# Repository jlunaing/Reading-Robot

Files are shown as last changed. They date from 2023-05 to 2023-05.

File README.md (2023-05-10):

### Reading-Robot
A socially assistive robot that can help students with reading practice. For 
instructions on how to use the system, see [user guide](user_guide.md).

## Background

There is an insufficient availability of human experts to assist students in 
reading competency and comprehension. The goal of this porject is to create an 
socially assistive robot that can be used by therapists, teachers, and parents 
to help children and adults develop and practice reading comprehension skills 
while they do not have access to specialists. This robot enables the user to 
improve their reading skills without an educator present and allows educators to 
review the student's performance remotely. 

The design includes a robot and a phone running an app. The basic tasks that the
robot performs is to give instructions for the reading sessions and prompts the
student to start reading. The robot then records the passage read to allow a 
teacher or therapist to review it at a later time. Then, the robot asks 
questions based on the reading and gives constructive feedback based on the 
correctness of the responses. During the interaction, the robot has the ability
to tilt the phone back and forth, wiggle its antennas, and show different faces
on its LED screen. This gives the interaction with the user more embodiment.

## Making a Reading Robot

### Part List
To make one of this robots, the following parts are needed:

#### General parts:
- 3D printed parts (see [CAD files](src/hardware/cad/solidworks/))
- Android phone (1)
- Bluetooth headset (optional) (1)
- Pimoroni Unicorn Hat HD LED array (1)					

#### Actuation:
- TowerPro MG995 Digital servo motor (1)				
- Uxcell 6V DC motor, 100-rpm (1)	
- Adafruit TB6612 motor driver board (1)					
- 6455K13 plastic ball bearing (2)					
- RB-Tib-11 Lynxmotion servo timing belt pulley (2)					
- 1254N22 MXL timing belt pulley (1)	

#### Fasteners:
- Tapered heat-set inserts:
  - 2-56 thread size (93365A110)			
  - 4-40 thread size (93365A120)
- Screws:
  - 18-8 screw 1/2'' long (91772A110)
  - 2-56 screw 11/32'' long (91772A506)
  - 2-56 screw 3/16'' long (91772A076)
  - 4-40 screw 3/4'' long (91772A113)			
- Neodymium magnet 1/4'' (5862K103) (8)
- 18-8 binding barrel & screw (99637A307) (1)
- Nylon spacers (90176A114)
- 5/8'' Long Dowel Pin (98381A539)					
- 2 – 1/8'' Long Dowel Pin (98381A325)					

#### Electronics:
- Raspberry Pi 4 + SD card
- Custom PCB for power distribution (see [board files](src/hardware/pcb/))
- 40-pin connector (S9200-ND) (2)
- USB-C breakout board (1568-1958-ND)
- JST RCY connector, 2-pin (PRT-10501)					
- JST jumper 2-wire (PRT-09914)					
- JST jumper 3-wire (PRT-09915)

### Power:
- AUKEY USB-C 2 port charger					
- AC adapter/power supply (2)					
- USB 3.1 type C M-F data extension cable (2)					

The assembly of the robot can be facilitated by refering to the assembly drawings
or the [CAD files](src/hardware/cad/solidworks/). Some reference images are 
included below.

<p align="center">
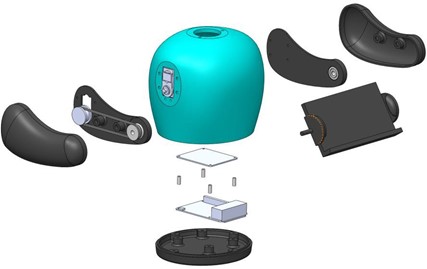
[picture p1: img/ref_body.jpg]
Body assembly
    
</p>

<p align="center">
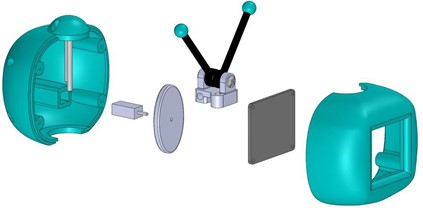
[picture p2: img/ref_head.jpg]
Head assembly
    
</p>

### Code

See [source files](src/firmware/python/) for details.

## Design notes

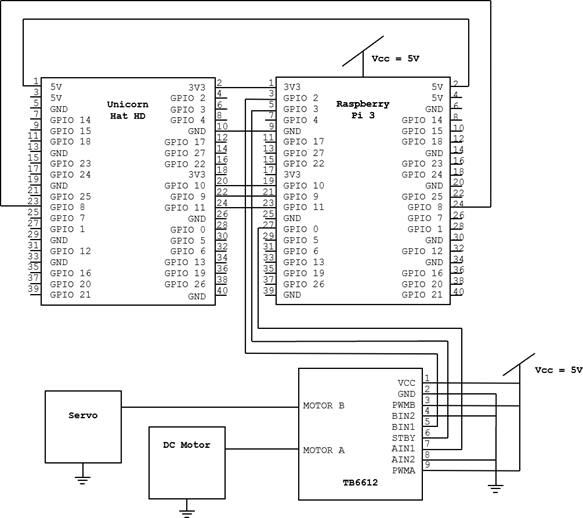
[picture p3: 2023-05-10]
img/ref_schematic.png

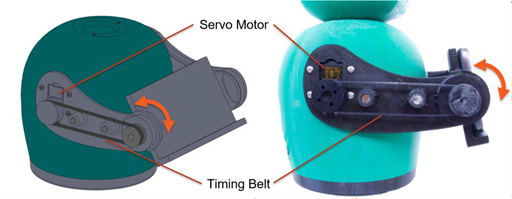
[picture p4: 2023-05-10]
img/ref_servo.png

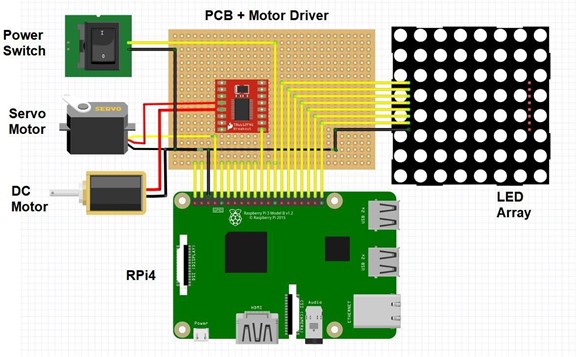
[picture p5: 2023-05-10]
img/ref_connections.jpg

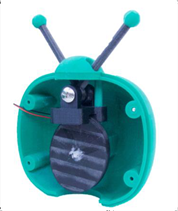
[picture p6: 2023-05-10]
img/ref_antenna_02.png

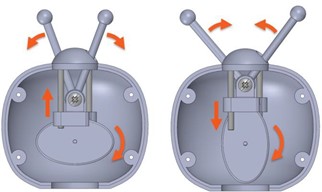
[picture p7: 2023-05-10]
img/ref_antenna_01.jpg

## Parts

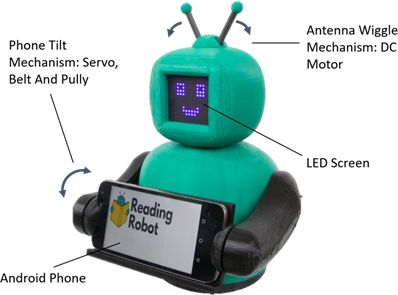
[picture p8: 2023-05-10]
img/ref_parts.png

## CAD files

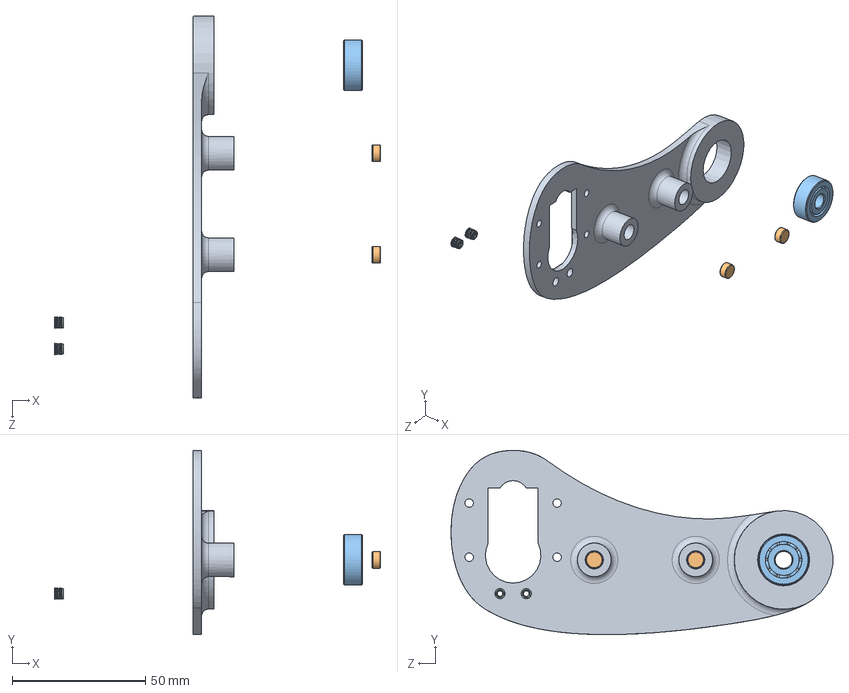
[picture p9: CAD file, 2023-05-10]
src/hardware/cad/solidworks/arm_base_right_assy.SLDASM
122.5 x 69.2 x 143.5 mm
5862K103_HIGH-PULL RARE EARTH MAGNETIC DISC x 2
6455K130_GENERAL PURPOSE PLASTIC BALL BEARING
arm_base_right
93365A120_HEAT-SET INSERTS FOR PLASTICS x 2

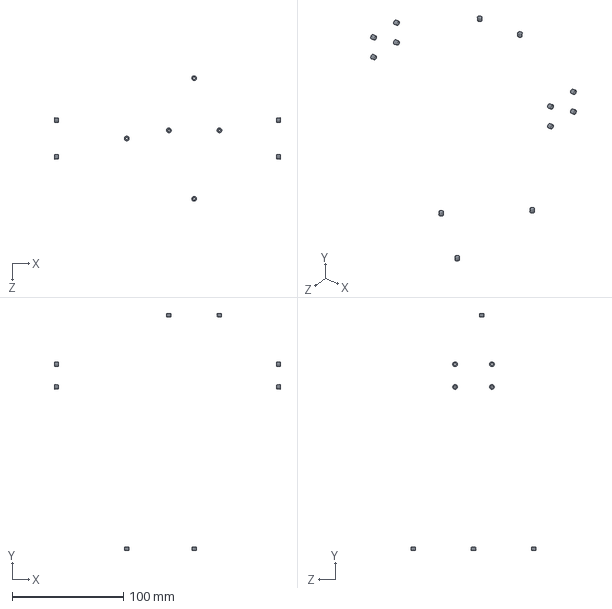
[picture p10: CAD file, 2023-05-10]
src/hardware/cad/solidworks/body_top_with_inserts.SLDASM
202.8 x 212.9 x 112.6 mm
93365A120_HEAT-SET INSERTS FOR PLASTICS x 13

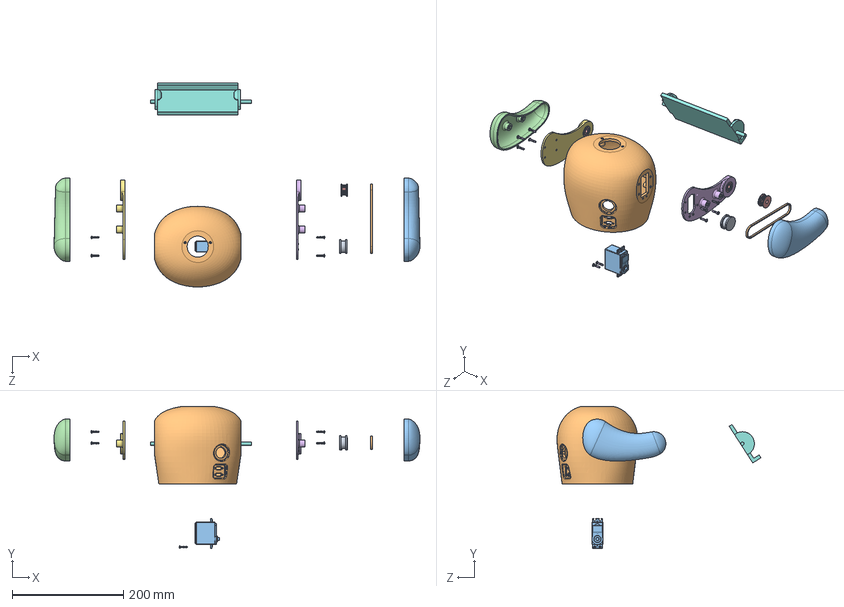
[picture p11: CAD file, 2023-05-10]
src/hardware/cad/solidworks/body_top_assy.SLDASM
658.0 x 255.6 x 366.7 mm
93365A120_HEAT-SET INSERTS FOR PLASTICS x 15
body_top
servomotor
5862K103_HIGH-PULL RARE EARTH MAGNETIC DISC x 8
6455K130_GENERAL PURPOSE PLASTIC BALL BEARING x 2
arm_base_right
arm_base_left
phone holder
servo_timing_belt_pulley
belt
arm_cover_right
arm_cover_left
1254N220_MXL SERIES LIGHTWEIGHT TIMING BELT PULLEY
91772A110_18-8 SS PAN HEAD PHILLIPS MACHINE SCREW x 10

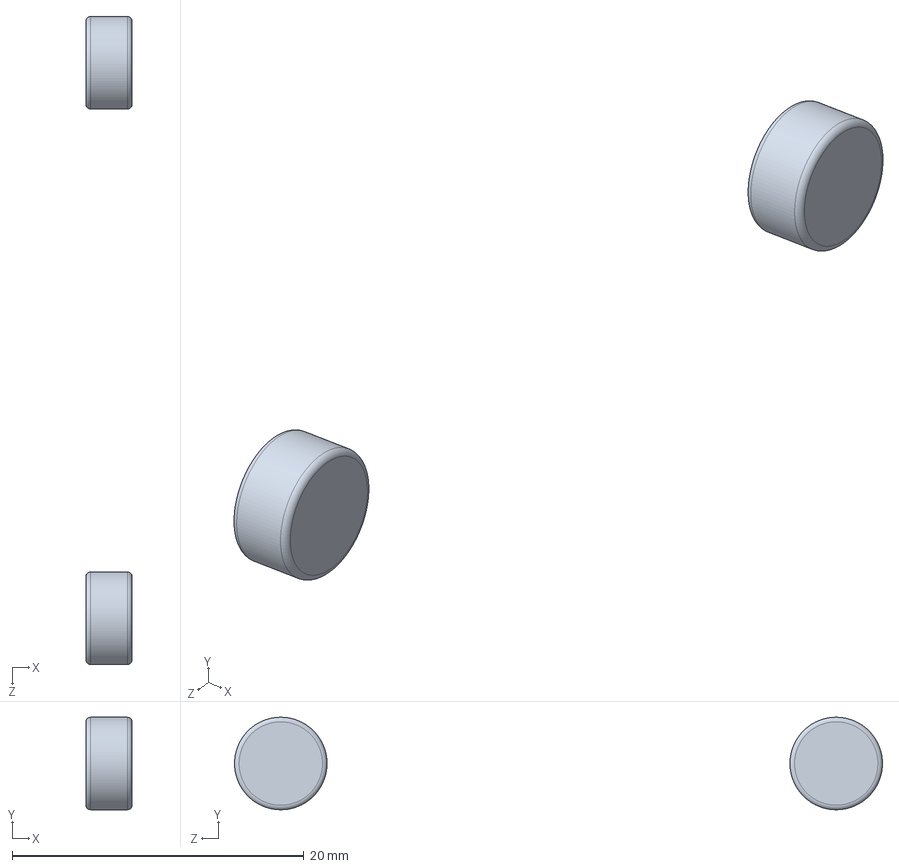
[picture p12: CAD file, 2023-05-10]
src/hardware/cad/solidworks/arm_cover_left_assy.SLDASM
3.17 x 6.35 x 44.5 mm
5862K103_HIGH-PULL RARE EARTH MAGNETIC DISC x 2

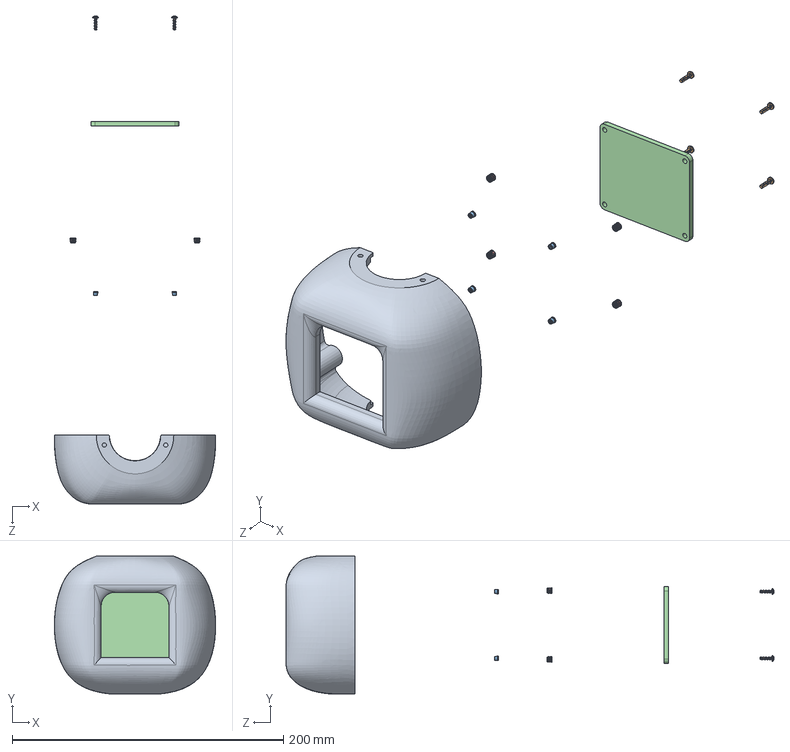
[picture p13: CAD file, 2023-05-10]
src/hardware/cad/solidworks/head_front_assy.SLDASM
119.0 x 101.6 x 359.9 mm
head_front
91772A506_PASSIVATED 18-8 SS PAN HEAD PHILLIPS SCREW x 4
93365A110_HEAT-SET INSERTS FOR PLASTICS x 4
led_screen
93365A120_HEAT-SET INSERTS FOR PLASTICS x 4

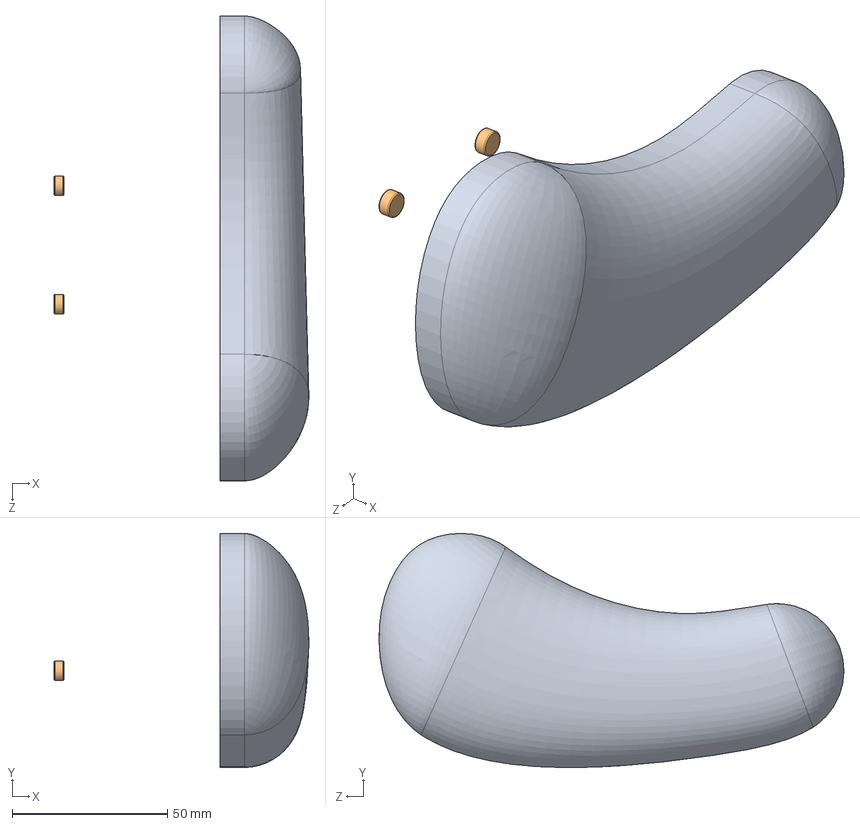
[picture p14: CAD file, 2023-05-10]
src/hardware/cad/solidworks/arm_cover_right_assy.SLDASM
82.0 x 75.3 x 149.6 mm
arm_cover_right
5862K103_HIGH-PULL RARE EARTH MAGNETIC DISC x 2

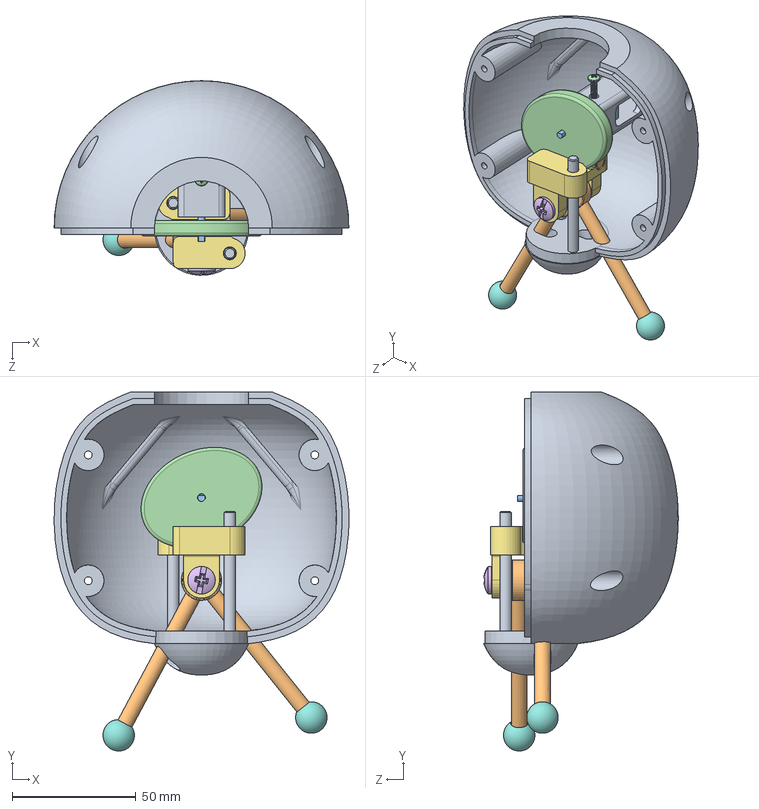
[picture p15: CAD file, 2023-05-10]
src/hardware/cad/solidworks/head_back_assy.SLDASM
119.0 x 144.9 x 78.6 mm
head_back
antenna_bottom x 2
dc_motor
crank
98002A709_STEEL BINDING SCREWS
99637A212_18-8 STAINLESS STEEL BINDING BARREL
antenna fixture
antenna_top x 2
98381A325_DOWEL PIN x 2
98381A539_ALLOY STEEL DOWEL PIN x 2
93365A120_HEAT-SET INSERTS FOR PLASTICS
91772A110_18-8 SS PAN HEAD PHILLIPS MACHINE SCREW

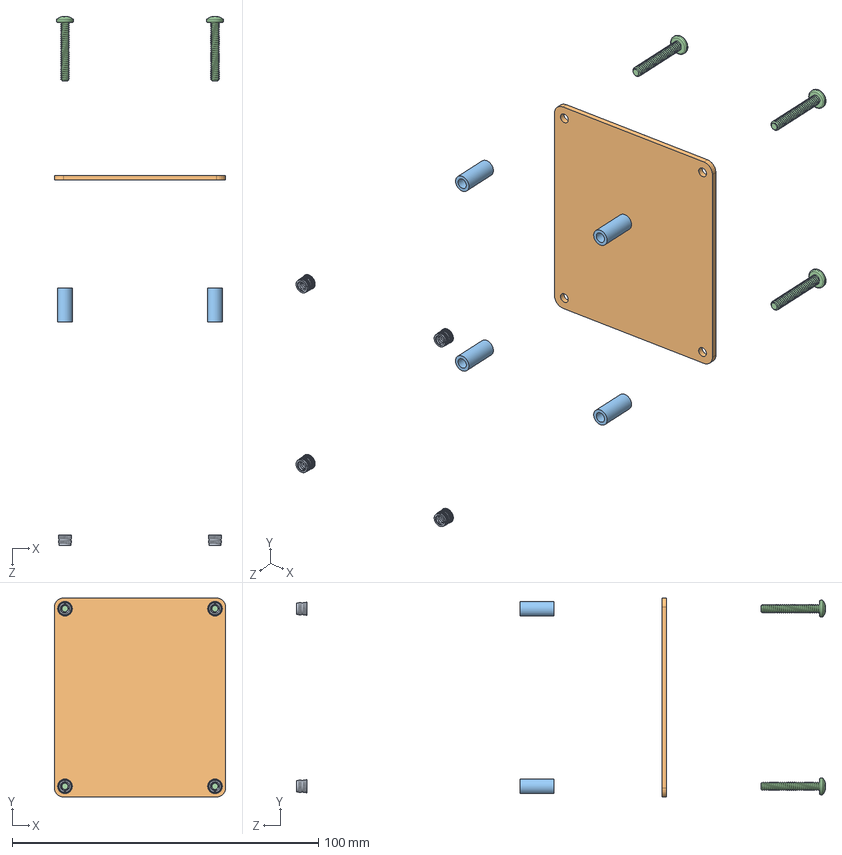
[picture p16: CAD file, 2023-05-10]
src/hardware/cad/solidworks/body_bottom_assy.SLDASM
56.0 x 65.0 x 172.8 mm
93365A120_HEAT-SET INSERTS FOR PLASTICS x 4
PCB
90176A114_NYLON UNTHREADED SPACERS x 4
91772A113_18-8 SS PAN HEAD PHILLIPS MACHINE SCREW x 4

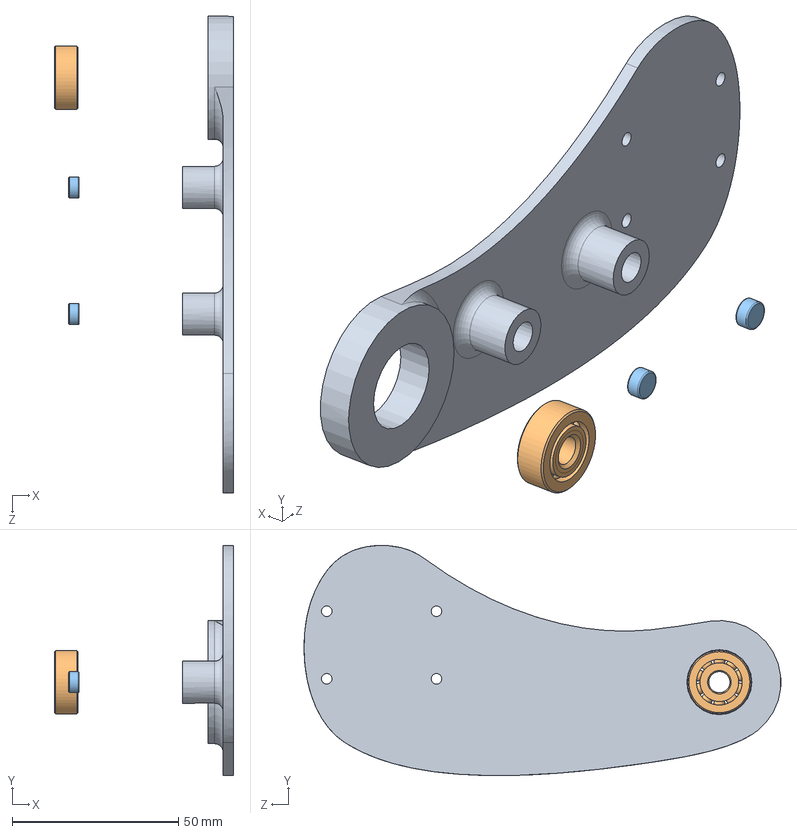
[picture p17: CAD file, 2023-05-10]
src/hardware/cad/solidworks/arm_base_left_assy.SLDASM
54.0 x 69.2 x 143.5 mm
arm_base_left
6455K130_GENERAL PURPOSE PLASTIC BALL BEARING
5862K103_HIGH-PULL RARE EARTH MAGNETIC DISC x 2

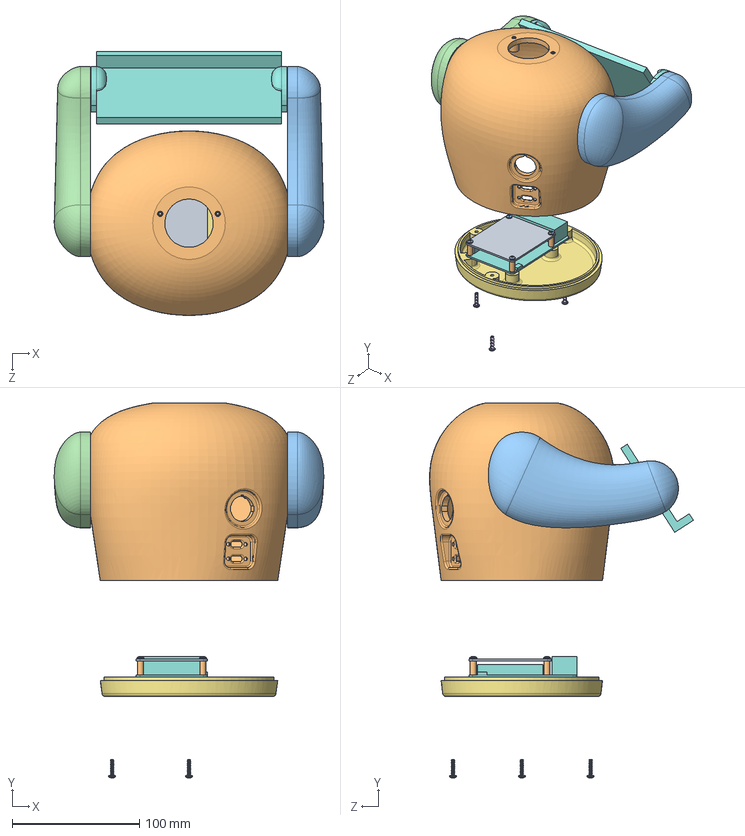
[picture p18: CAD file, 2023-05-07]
src/hardware/cad/solidworks/body_main.SLDASM
212.1 x 294.9 x 207.6 mm
93365A120_HEAT-SET INSERTS FOR PLASTICS x 20
body_top_3
kiso
5862K103_HIGH-PULL RARE EARTH MAGNETIC DISC x 8
6455K130_GENERAL PURPOSE PLASTIC BALL BEARING x 2
arm_base_right_3
arm_base_left_2
phone holder_3
Servo Timing Belt Pulley
Belt
arm_cover_right_2
arm_cover_left_2
1254N220_MXL SERIES LIGHTWEIGHT TIMING BELT PULLEY
91772A110_18-8 SS PAN HEAD PHILLIPS MACHINE SCREW x 13
body_bottom_4
Rasberry pi
PCB
90176A114_NYLON UNTHREADED SPACERS x 4
91772A113_18-8 SS PAN HEAD PHILLIPS MACHINE SCREW x 4

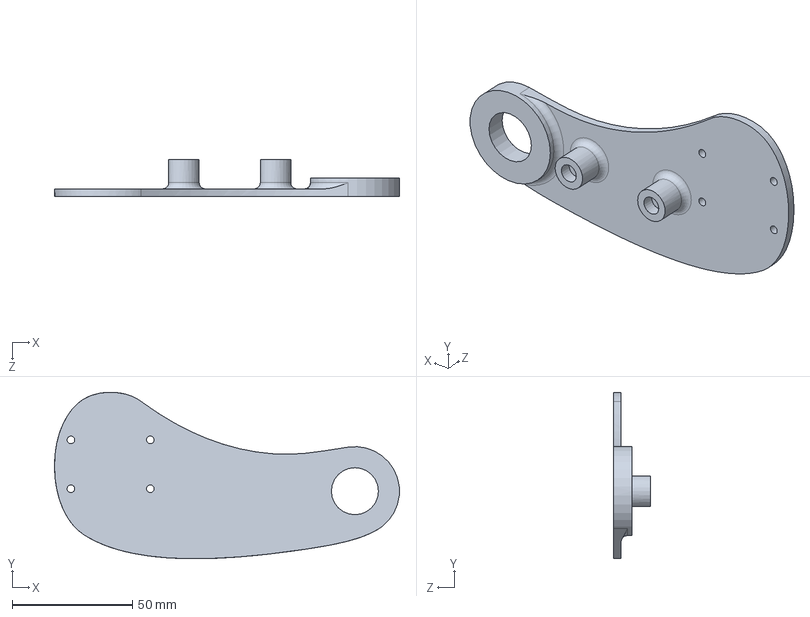
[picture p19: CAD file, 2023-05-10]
src/hardware/cad/solidworks/arm_base_left.SLDPRT
143.5 x 69.2 x 15.4 mm

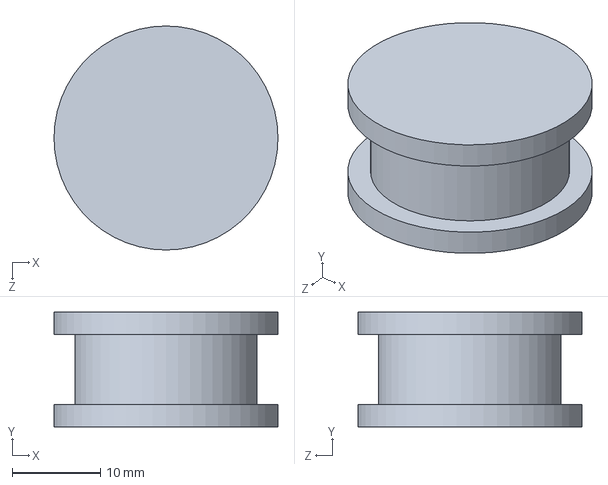
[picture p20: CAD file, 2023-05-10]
src/hardware/cad/solidworks/servo_timing_belt_pulley.SLDPRT
25.4 x 13.0 x 25.4 mm

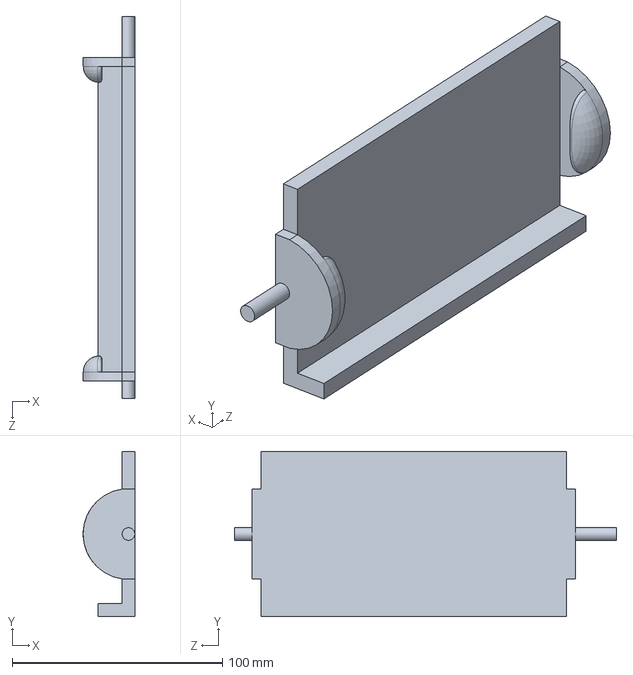
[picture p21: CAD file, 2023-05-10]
src/hardware/cad/solidworks/phone holder.SLDPRT
24.6 x 78.5 x 181.6 mm

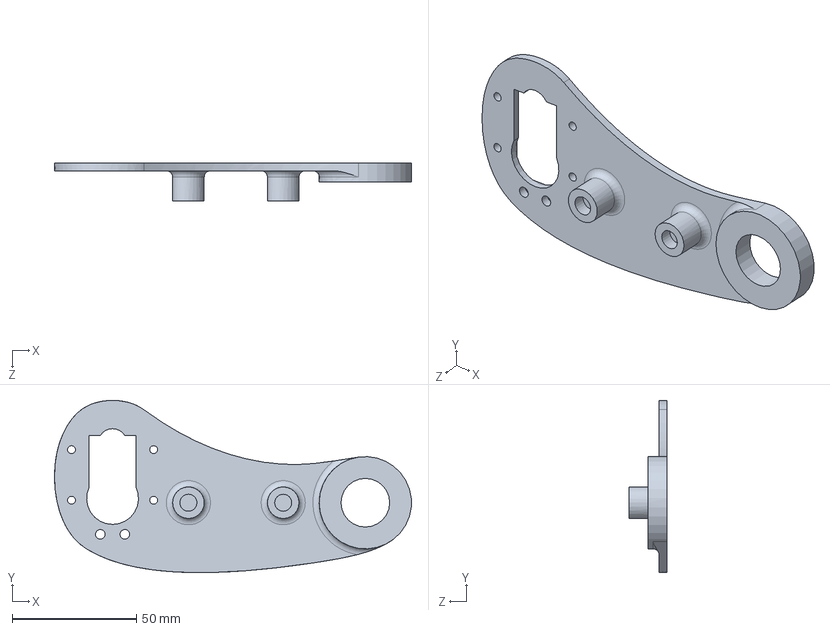
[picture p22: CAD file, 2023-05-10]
src/hardware/cad/solidworks/arm_base_right.SLDPRT
143.5 x 69.2 x 15.4 mm

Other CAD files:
src/hardware/cad/solidworks/PCB.SLDPRT
src/hardware/cad/solidworks/arm_cover_right.SLDPRT
src/hardware/cad/solidworks/servomotor.SLDPRT
src/hardware/cad/solidworks/belt.SLDPRT
src/hardware/cad/solidworks/1254N220_MXL SERIES LIGHTWEIGHT TIMING BELT PULLEY.SLDPRT
src/hardware/cad/solidworks/5862K103_HIGH-PULL RARE EARTH MAGNETIC DISC.SLDPRT
src/hardware/cad/solidworks/6455K130_GENERAL PURPOSE PLASTIC BALL BEARING.SLDPRT
src/hardware/cad/solidworks/90176A114_NYLON UNTHREADED SPACERS.SLDPRT
src/hardware/cad/solidworks/91772A110_18-8 SS PAN HEAD PHILLIPS MACHINE SCREW.SLDPRT
src/hardware/cad/solidworks/91772A113_18-8 SS PAN HEAD PHILLIPS MACHINE SCREW.SLDPRT
src/hardware/cad/solidworks/91772A506_PASSIVATED 18-8 SS PAN HEAD PHILLIPS SCREW.SLDPRT
src/hardware/cad/solidworks/93365A110_HEAT-SET INSERTS FOR PLASTICS.SLDPRT
src/hardware/cad/solidworks/93365A120_HEAT-SET INSERTS FOR PLASTICS.SLDPRT
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

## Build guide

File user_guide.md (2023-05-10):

### User Guide for the Reading Robot

1. [Set up](#set-up)
2. [Troubleshooting](#troubleshooting)

## Set up
1. Locate female USB-C ports on the back of the robot. The bottom port is dedicated to the Raspberry Pi and the one above is connected to the power distribution board.

<p align="center">
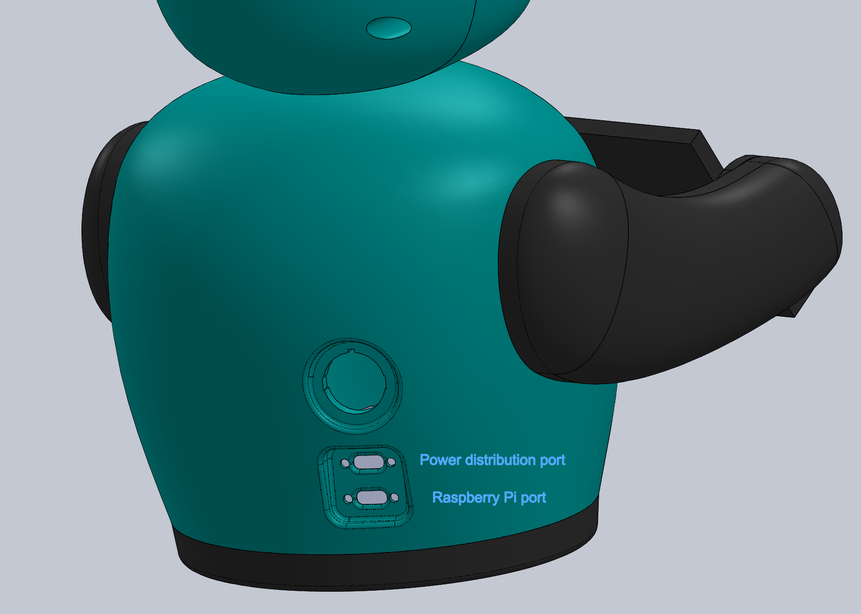
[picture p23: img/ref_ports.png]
Input ports for the robot.
    
</p>

2. Connect the Raspberry Pi port to power. To verify, you will see a red glow inside the robot.
3. Wait for a blue, happy face to appear on LED Array. This is important as it is an indicator that the serial port service has been registered and that GPIOs are reset.
4. Connect the power distribution board to power. 
5. If using a wireless headset, connect it to the Android through Bluetooth. During the first time, you will have to pair the headset to the phone. Later usage should connect the headset to the phone seamlessly.
   
Once this has all been completed, the robot should be ready to go. Now, you can open the phone app.

1. Open the [app](src/firmware/appinventor/) on the phone.
2. Once opened, a “connected” notification should show up fairly quickly to let the user know they are connected to Bluetooth. If this does not happen, you can press the robot's picture once the robot finishes its introduction dialogue. 
    - If a face change does not occur after introduction, Bluetooth is not connected and a notification error will pop up on the app. 
    - Refer to the next section, troubleshooting.
3. When the connected notifier appears, the app is ready to go. The user will read (press "begin reading" to start reading and "stop reading" to proceed to the next part) and answer questions afterwards (press "question" button).

<p align="center">
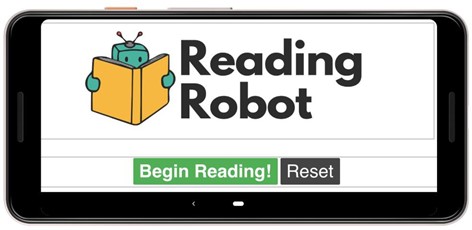
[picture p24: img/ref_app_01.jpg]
Android app intro screen.
    
</p>

After the session is over:

1. Close the app and make sure to end it completely.
2. Turn off the PCB *first*. The robot does not like it when you power down the Raspberry Pi first.
   - This is currently an issue because the PCB has its I/O pins for the motors routed to the pins on the RPi that give a 3.3-V voltage on startup.
   - This is also the same reason why the PCB is turned on after the RPi’s startup sequence. 
3. Turn off the Raspberry Pi.

Optional step for users, parents, instructors, and educators:

1. To playback the audio file that was generated from the app stored in the phone, go to the storage settings of your phone and search for the generated "Reading Robot Study 2020" folder. The default file name is `mysound.3gp`. Make sure to look at the time associated with the file creation to see which corresponds to which user.
2. To view the text file that was generated from the app during the human-robot interaction, go to the storage settings and look for the corresponding `.txt` file.

## Troubleshooting

This section discusses some of the problems that could be encountered while
working with the robot as it relates to the **Bluetooth connection**.

If the Bluetooth connection doesn’t happen, it could be for a multitude of reasons. The first possible error is that the Raspberry Pi is no longer paired with the Android phone. To check for this, go to your phone settings and check for the Bluetooth paired devices. Under the “paired devices” section, there should a paired device corresponding to the Raspberry Pi used.

If this device is not there or no longer paired, you must direct your attention to the Raspberry Pi. Unscrew the bottom of the robot and connect to the Pi. After the Pi has turned on, it should show up in the “available devices” section of the
phone's Bluetooth settings. Click on Raspberry Pi device on the phone. A notification should appear on the Pi’s home screen and phone screen for a pairing request. Press confirm. The device should now be paired, and the Bluetooth connection should work between the Pi and the app.

You can hardcode the process in the above paragraph as well in terminal: `bluetoothctl` $\to$ `agent on` $\to$ `discoverable on` $\to$ `scan on`. The phone's bluetooth address should appear. Pair it with the Pi and that should work.

If the Raspberry Pi is still paired, there are two reasons why there is no bluetooth connection between the devices. ***First***, the bluetooth address might be incorrect from the development environment (Kodular) side of things. Double check and make sure the address is correct. You can find the address of your Raspberry Pi in terminal using the `hciconfig` command in the terminal. Look for the address followed by `BD Address`.

If the address is correct, then the *second* possibility is that the user troubleshooting is not waiting long enough to connect the devices. After the blue, happy face screen appears, wait an additional 15-30 seconds.

If none of this works, there could be an issue with the serial port service registering. This is a Python script that runs on startup and gives access to the Raspberry Pi serial ports. The name of the script is `register.py` and can be found with all the other scripts the robot utilizes to function. You can check to see if it ran on startup as well as anything else that happens between the Android and Pi. Look up the `/home/pi/logs` directory. The file called `cronlog` will give you a log of what happens during the interaction between the phone and Raspberry Pi. This will be pretty important when troubleshooting the robot and changing the script.

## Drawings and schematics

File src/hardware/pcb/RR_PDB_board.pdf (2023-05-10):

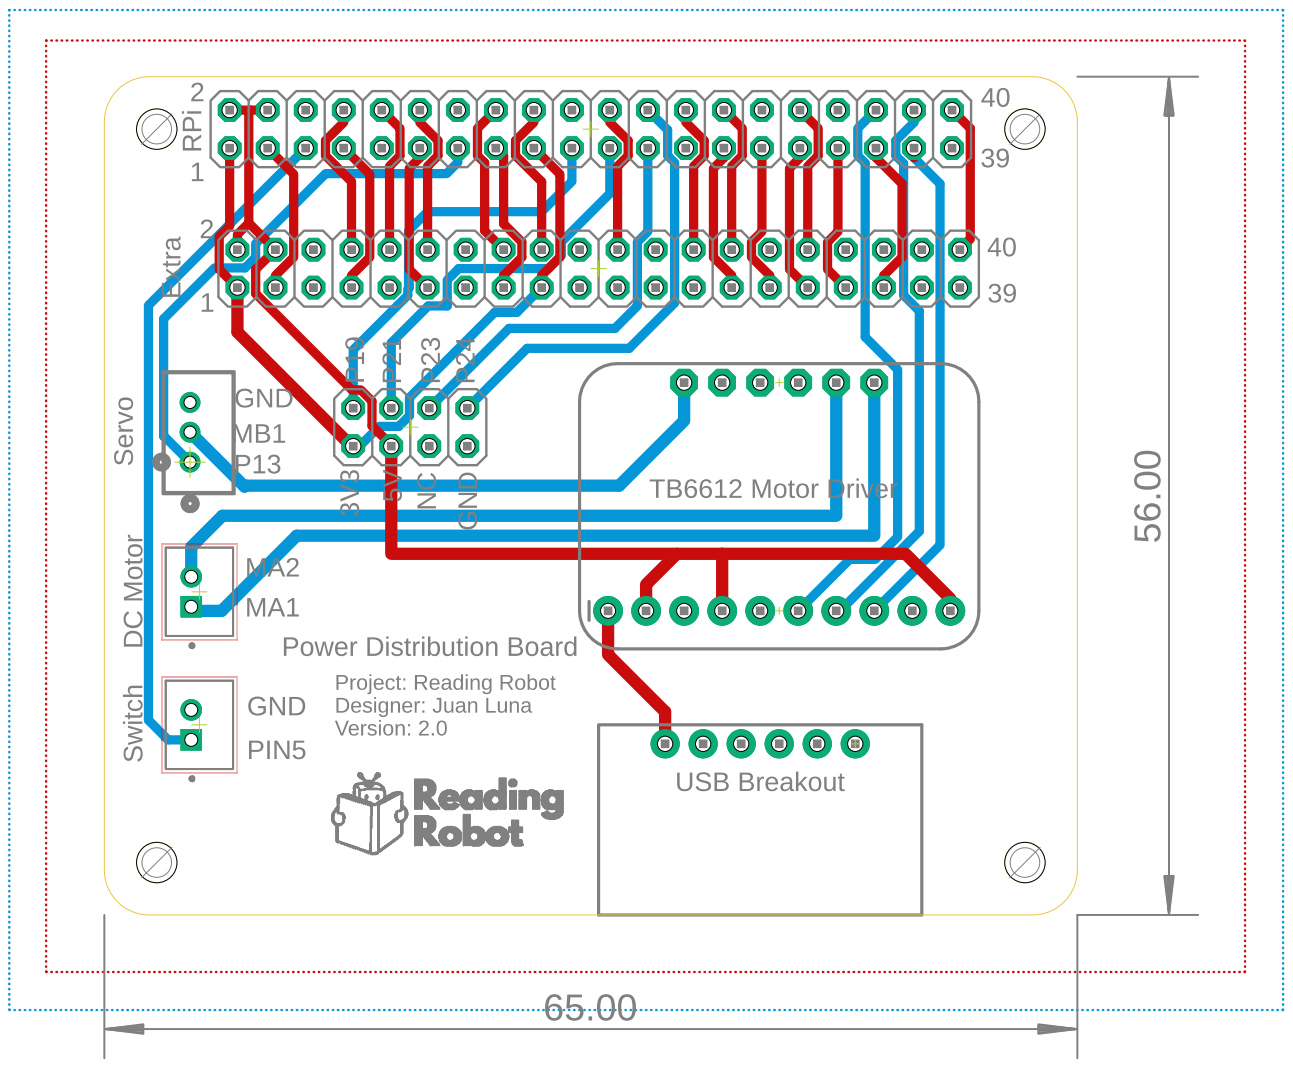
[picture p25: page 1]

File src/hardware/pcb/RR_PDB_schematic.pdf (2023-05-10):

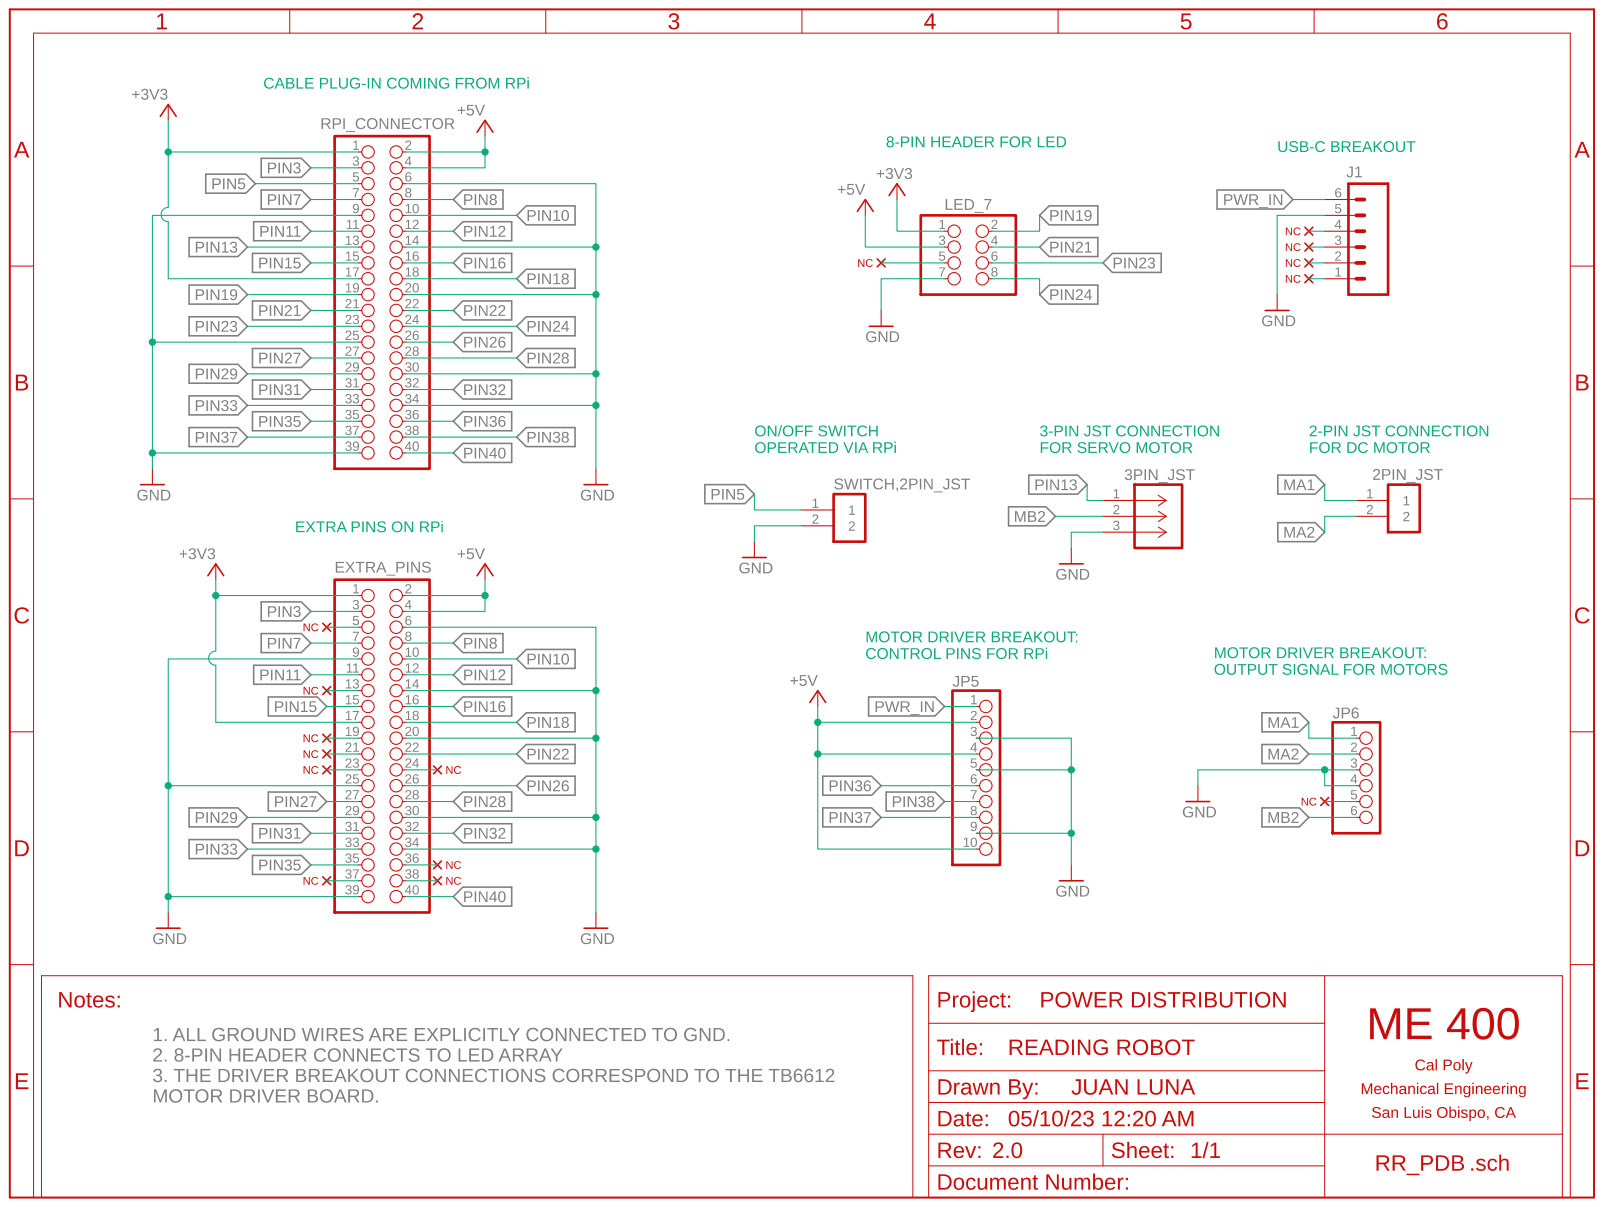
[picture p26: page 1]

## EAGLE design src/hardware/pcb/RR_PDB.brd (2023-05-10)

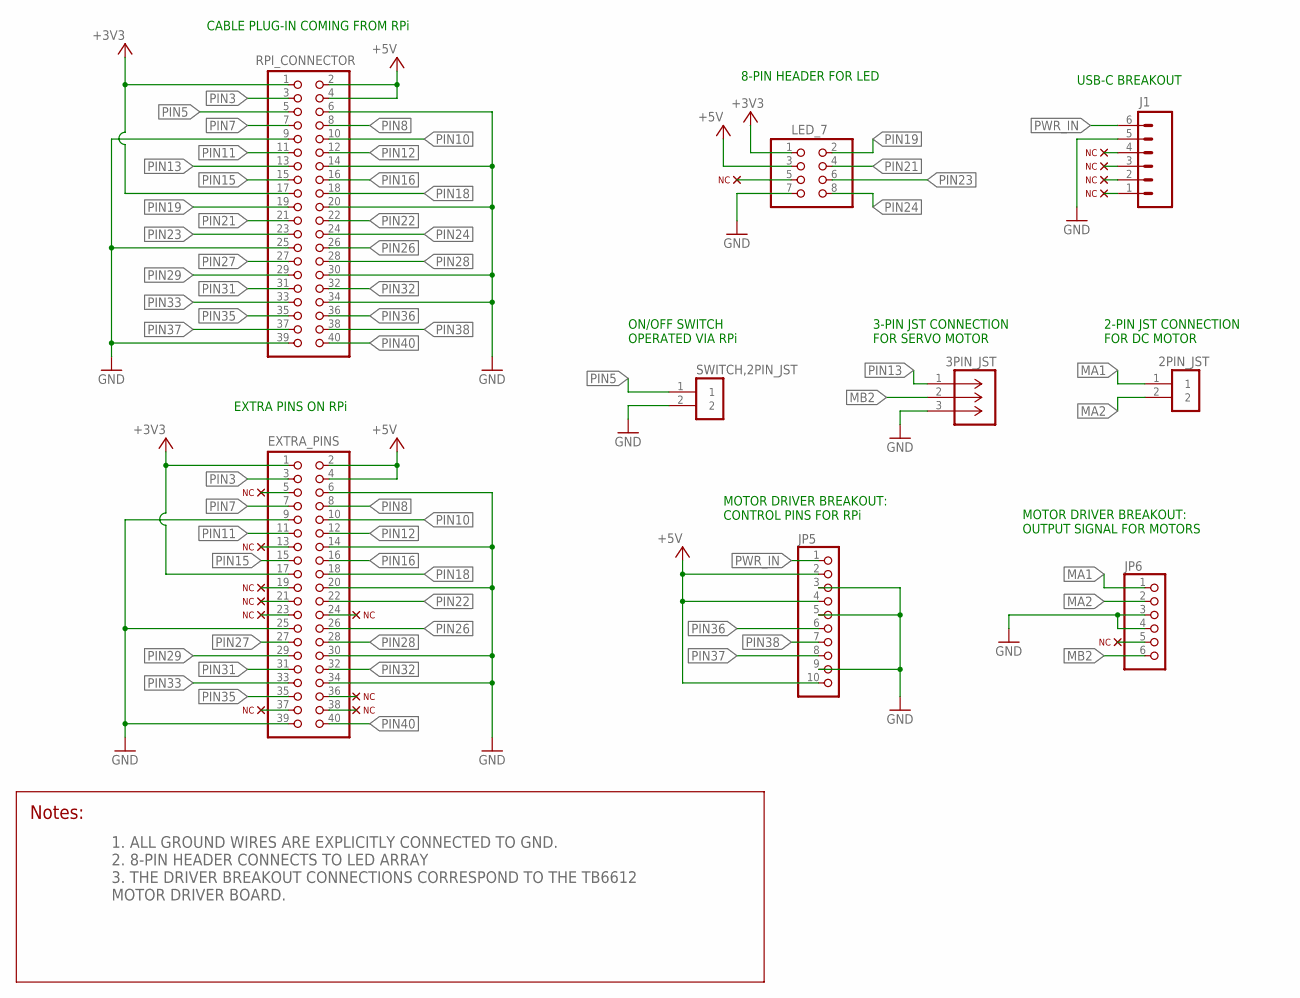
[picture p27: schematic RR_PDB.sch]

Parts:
2PIN_JST: B2B-PH-K-S(LF)(SN); JST_B2B-PH-K-S(LF)(SN)
3PIN_JST: B3B-PH-K-S(LF)(SN); CONN_B3B-PH-K-S(LF)(SN)_JST
EXTRA_PINS: PINHD-2X20; 2X20
J1: CONN_06NO_SILK_NO_POP; 1X06_NO_SILK
JP5: HEADER-1X10THICKER; 1X10_ROUND_76
JP6: PINHD-1X6CB; 1X06-CLEANBIG
LED_7: PINHD-2X4; 2X04
RPI_CONNECTOR: PINHD-2X20; 2X20
SWITCH,2PIN_JST: B2B-PH-K-S(LF)(SN); JST_B2B-PH-K-S(LF)(SN)

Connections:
+3V3: EXTRA_PINS.1, EXTRA_PINS.17, LED_7.1, RPI_CONNECTOR.1, RPI_CONNECTOR.17
+5V: EXTRA_PINS.2, EXTRA_PINS.4, JP5.2, JP5.4, JP5.10, LED_7.3, RPI_CONNECTOR.2, RPI_CONNECTOR.4
CC1: J1.4
CC2: J1.1
D+: J1.2
D-: J1.3
GND: 3PIN_JST.3, EXTRA_PINS.6, EXTRA_PINS.9, EXTRA_PINS.14, EXTRA_PINS.20, EXTRA_PINS.25, EXTRA_PINS.30, EXTRA_PINS.34, EXTRA_PINS.39, J1.5, JP5.3, JP5.5, JP5.9, JP6.3, JP6.4, LED_7.7, RPI_CONNECTOR.6, RPI_CONNECTOR.9, RPI_CONNECTOR.14, RPI_CONNECTOR.20, RPI_CONNECTOR.25, RPI_CONNECTOR.30, RPI_CONNECTOR.34, RPI_CONNECTOR.39, SWITCH,2PIN_JST.2
MA1: 2PIN_JST.1, JP6.1
MA2: 2PIN_JST.2, JP6.2
MB2: 3PIN_JST.2, JP6.6
PIN3: EXTRA_PINS.3, RPI_CONNECTOR.3
PIN5: RPI_CONNECTOR.5, SWITCH,2PIN_JST.1
PIN7: EXTRA_PINS.7, RPI_CONNECTOR.7
PIN8: EXTRA_PINS.8, RPI_CONNECTOR.8
PIN10: EXTRA_PINS.10, RPI_CONNECTOR.10
PIN11: EXTRA_PINS.11, RPI_CONNECTOR.11
PIN12: EXTRA_PINS.12, RPI_CONNECTOR.12
PIN13: 3PIN_JST.1, RPI_CONNECTOR.13
PIN15: EXTRA_PINS.15, RPI_CONNECTOR.15
PIN16: EXTRA_PINS.16, RPI_CONNECTOR.16
PIN18: EXTRA_PINS.18, RPI_CONNECTOR.18
PIN19: LED_7.2, RPI_CONNECTOR.19
PIN21: LED_7.4, RPI_CONNECTOR.21
PIN22: EXTRA_PINS.22, RPI_CONNECTOR.22
PIN23: LED_7.6, RPI_CONNECTOR.23
PIN24: LED_7.8, RPI_CONNECTOR.24
PIN26: EXTRA_PINS.26, RPI_CONNECTOR.26
PIN27: EXTRA_PINS.27, RPI_CONNECTOR.27
PIN28: EXTRA_PINS.28, RPI_CONNECTOR.28
PIN29: EXTRA_PINS.29, RPI_CONNECTOR.29
PIN31: EXTRA_PINS.31, RPI_CONNECTOR.31
PIN32: EXTRA_PINS.32, RPI_CONNECTOR.32
PIN33: EXTRA_PINS.33, RPI_CONNECTOR.33
PIN35: EXTRA_PINS.35, RPI_CONNECTOR.35
PIN36: JP5.6, RPI_CONNECTOR.36
PIN37: JP5.8, RPI_CONNECTOR.37
PIN38: JP5.7, RPI_CONNECTOR.38
PIN40: EXTRA_PINS.40, RPI_CONNECTOR.40
PWR_IN: J1.6, JP5.1

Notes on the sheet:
MOTOR DRIVER BREAKOUT: OUTPUT SIGNAL FOR MOTORS
MOTOR DRIVER BREAKOUT: CONTROL PINS FOR RPi
2-PIN JST CONNECTION FOR DC MOTOR
3-PIN JST CONNECTION FOR SERVO MOTOR
CABLE PLUG-IN COMING FROM RPi
ON/OFF SWITCH OPERATED VIA RPi
EXTRA PINS ON RPi
8-PIN HEADER FOR LED
USB-C BREAKOUT
1. ALL GROUND WIRES ARE EXPLICITLY CONNECTED TO GND. 2. 8-PIN HEADER CONNECTS TO LED ARRAY 3. THE DRIVER BREAKOUT CONNECTIONS CORRESPOND TO THE TB6612 MOTOR DRIVER BOARD.

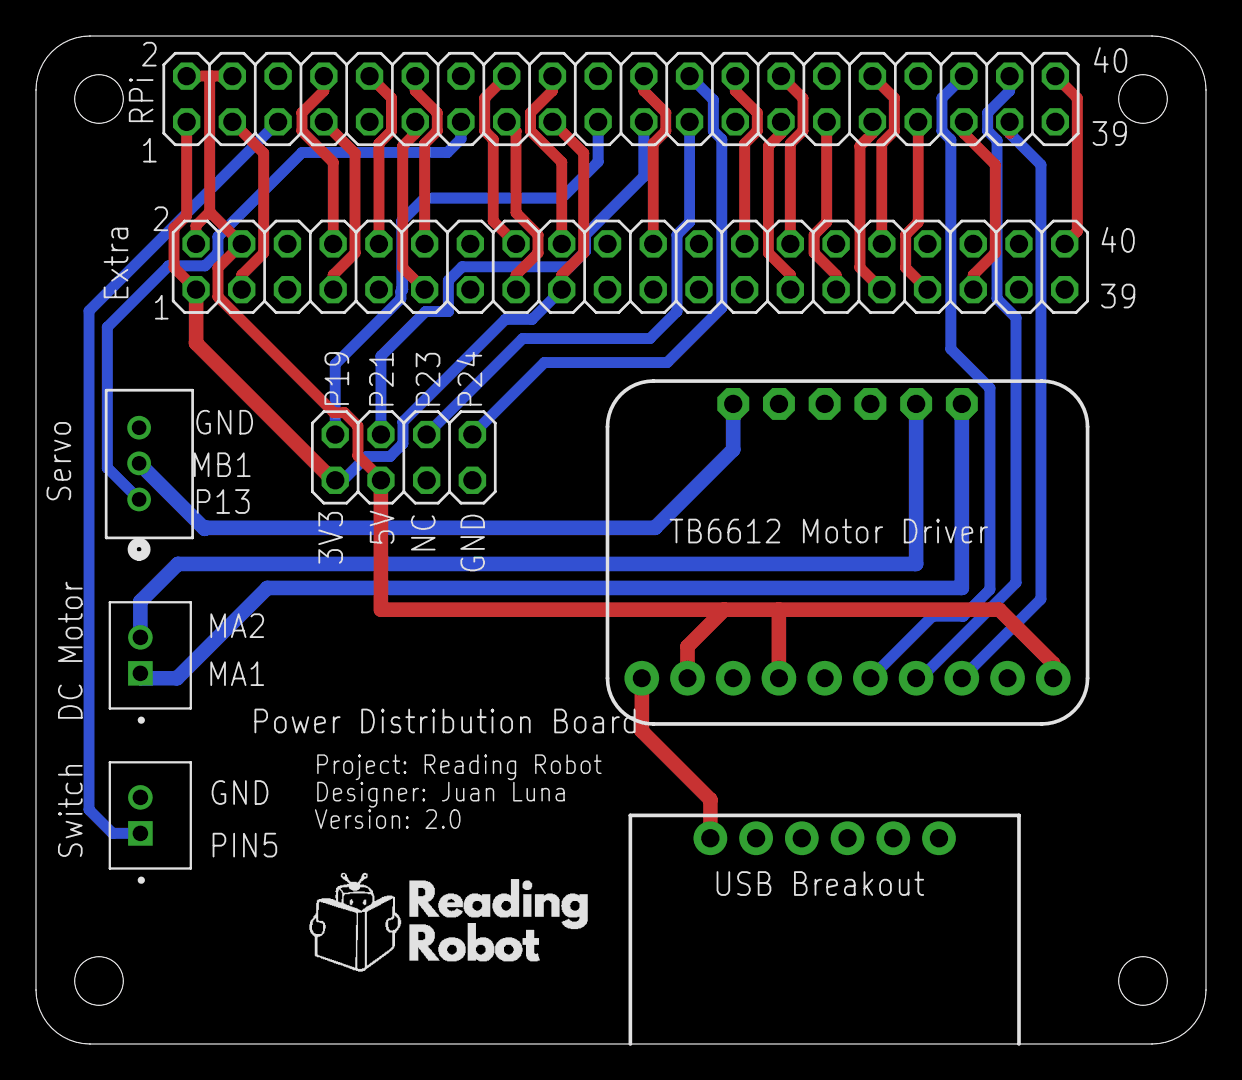
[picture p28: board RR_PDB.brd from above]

Board: 2 copper layers, 65.0 x 56.0 mm, 9 parts (0 on the bottom side), 35 nets.

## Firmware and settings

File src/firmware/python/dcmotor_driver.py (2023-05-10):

'''!    @file       dcmotor_driver.py
        @brief      Motor testing
        @details    This code will need to take in the following values: 
                    time for antenna move and position for servo. May need to 
                    saturate duty cycle.
        @author     Juan Luna
        @date       2021-01-28 Created
'''

import RPi.GPIO as GPIO
from time import sleep



# Pins for Motor Driver Inputs 
DCMotor = 0 #GPIO 0

ServoMotor = 1 #GPIO 1
ServoMotorEN = 2 #GPIO 2
STBYPin = 3 #GPIO 3

def setup():
    GPIO.setmode(GPIO.BCM)              # GPIO Numbering
    GPIO.setup(DCMotor,GPIO.OUT)  # All pins as Outputs
    
    GPIO.setup(ServoMotor,GPIO.OUT)
    GPIO.setup(ServoMotorEN,GPIO.OUT)
    servo_ctr = GPIO.PWM(ServoMotor, 50) #channel = ServoMotor, frequency=50Hz
    
    
    
    GPIO.setup(STBYPin,GPIO.OUT)   #enable motors
    GPIO.output(STBYPin,GPIO.HIGH)
 
def move_antenna():
    # Going forwards
    GPIO.output(DCMotor,GPIO.HIGH)
 
    sleep(5) # will need to remove this for cooperative multitasking
    # stop the motor after t= 5 seconds
    GPIO.output(DCMotor,GPIO.LOW)

def move_arms():
    # Going forwards
    GPIO.output(ServoMotorEN,GPIO.HIGH)
    servo_ctr.start(50) #start pwm signal at 50 duty cycle
    
 
    sleep(1) # will need to remove this for cooperative multitasking
    # stop the motor after some delay
     
    servo_ctr.ChangeDutyCycle (0) # move back to original position
    
    sleep(1) #allow time for movement
    servo_ctr.stop() #start pwm signal at 0 duty cycle
    

def destroy():  
    GPIO.cleanup() #set all ports back to input to protect



if __name__ == '__main__':     # Program start from here
    setup()
    try:
            move_antenna()
            move_arms()
    except KeyboardInterrupt:
        destroy()

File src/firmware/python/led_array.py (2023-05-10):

'''!    @file   led_array.py
        @brief  Different faces for the robot using LED screen
        @author Juan Luna
        @date   2021-05-26 Created
'''

import unicornhathd as unicorn
import time
import colorsys
import numpy
import RPi.GPIO as GPIO

GPIO.setup(LED,GPIO.OUT)  # initialize GPIO-21 (LED) as an output Pin
GPIO.output(LED,0)

server_socket = bluetooth.BluetoothSocket(bluetooth.RFCOMM)

port = 1
server_socket.bind(("",port))
server_socket.listen(1)

client_socket,address = server_socket.accept()
print ("Accepted connection from ",address)
while 1:

    data = client_socket.recv(1024)
    print ("Received: %s" % data)

    if (data == "0"):    # if '0' is sent from the Android App, turn OFF the LED
        print ("HAPPY FACE")
        set_pixels(face_happy)

    if (data == "1"):    # if '1' is sent from the Android App, turn OFF the LED
        print ("SAD FACE")
        set_pixels(face_down)

    if (data == "q"):
        print ("Quit")
        break

client_socket.close()
server_socket.close()

# eyes------------import RPi.GPIO as GPIO--------------------------

eyes_happy = [[0,0,0,0,1,0,0,0,0,0,0,1,0,0,0,0],
              [0,0,0,1,1,1,0,0,0,0,1,1,1,0,0,0],
              [0,0,0,1,1,1,0,0,0,0,1,1,1,0,0,0],
              [0,0,0,1,0,1,0,0,0,0,1,0,1,0,0,0]]

eyes_center = [[0,0,0,1,1,1,0,0,0,0,1,1,1,0,0,0],
               [0,0,0,1,0,1,0,0,0,0,1,0,1,0,0,0],
               [0,0,0,1,1,1,0,0,0,0,1,1,1,0,0,0],
               [0,0,0,1,1,1,0,0,0,0,1,1,1,0,0,0]]

eyes_down = [[0,0,0,1,1,1,0,0,0,0,1,1,1,0,0,0],
             [0,0,0,1,1,1,0,0,0,0,1,1,1,0,0,0],
             [0,0,0,1,1,1,0,0,0,0,1,1,1,0,0,0],
             [0,0,0,1,0,1,0,0,0,0,1,0,1,0,0,0]]

eyes_left = [[0,0,0,1,1,1,0,0,0,0,1,1,1,0,0,0],
             [0,0,0,0,1,1,0,0,0,0,0,1,1,0,0,0],
             [0,0,0,1,1,1,0,0,0,0,1,1,1,0,0,0],
             [0,0,0,1,1,1,0,0,0,0,1,1,1,0,0,0]]

eyes_right = [[0,0,0,1,1,1,0,0,0,0,1,1,1,0,0,0],
              [0,0,0,1,1,0,0,0,0,0,1,1,0,0,0,0],
              [0,0,0,1,1,1,0,0,0,0,1,1,1,0,0,0],
              [0,0,0,1,1,1,0,0,0,0,1,1,1,0,0,0]]

eyes_up = [[0,0,0,1,0,1,0,0,0,0,1,0,1,0,0,0],
           [0,0,0,1,1,1,0,0,0,0,1,1,1,0,0,0],
           [0,0,0,1,1,1,0,0,0,0,1,1,1,0,0,0],
           [0,0,0,1,1,1,0,0,0,0,1,1,1,0,0,0]]

eyes_big = [[0,0,0,1,1,1,0,0,0,0,1,1,1,0,0,0],
            [0,0,0,1,1,1,0,0,0,0,1,1,1,0,0,0],
            [0,0,0,1,1,1,0,0,0,0,1,1,1,0,0,0],
            [0,0,0,1,1,1,0,0,0,0,1,1,1,0,0,0]]

eyes_creepy = [[0,0,0,1,1,1,0,0,0,0,1,1,1,0,0,0],
               [0,0,0,0,1,0,0,0,0,0,0,1,0,0,0,0],
               [0,0,0,1,1,1,0,0,0,0,1,1,1,0,0,0],
               [0,0,0,1,1,1,0,0,0,0,1,1,1,0,0,0]]

# mouths

mouth_smile1 = [[0,0,0,0,0,1,0,0,0,0,1,0,0,0,0,0],
                [0,0,0,0,0,1,1,1,1,1,1,0,0,0,0,0],
                [0,0,0,0,0,0,1,1,1,1,0,0,0,0,0,0]]

mouth_smile2 = [[0,0,0,0,1,0,0,0,0,0,0,1,0,0,0,0],
                [0,0,0,0,0,1,1,1,1,1,1,0,0,0,0,0],
                [0,0,0,0,0,0,1,1,1,1,0,0,0,0,0,0]]

mouth_center = [[0,0,0,0,0,1,1,1,1,1,1,0,0,0,0,0],
                [0,0,0,0,0,0,1,1,1,1,0,0,0,0,0,0]]

mouth_left = [[0,0,0,0,0,1,1,1,1,1,1,0,0,0,0,0],
              [0,0,0,0,0,0,1,1,1,1,1,0,0,0,0,0]]

mouth_right = [[0,0,0,0,0,1,1,1,1,1,1,0,0,0,0,0],
               [0,0,0,0,0,1,1,1,1,1,0,0,0,0,0,0]]

mouth_straight = [[0,0,0,0,0,1,1,1,1,1,1,0,0,0,0,0],
                  [0,0,0,0,0,1,1,1,1,1,1,0,0,0,0,0]]

# noses

nose_beak = [[0,0,0,0,0,0,0,1,1,0,0,0,0,0,0,0],
             [0,0,0,0,0,0,0,1,1,0,0,0,0,0,0,0],
             [0,0,0,0,0,0,1,1,1,1,0,0,0,0,0,0]]

nose_center = [[0,0,0,0,0,0,0,1,1,0,0,0,0,0,0,0],
               [0,0,0,0,0,0,1,1,1,1,0,0,0,0,0,0],
               [0,0,0,0,0,0,1,1,1,1,0,0,0,0,0,0],
               [0,0,0,0,0,0,0,1,1,0,0,0,0,0,0,0]]

nose_down = [[0,0,0,0,0,0,1,1,1,1,0,0,0,0,0,0],
             [0,0,0,0,0,0,1,1,1,1,0,0,0,0,0,0],
             [0,0,0,0,0,0,0,1,1,0,0,0,0,0,0,0]]

nose_left = [[0,0,0,0,0,0,0,1,1,0,0,0,0,0,0,0],
             [0,0,0,0,0,0,1,1,1,0,0,0,0,0,0,0],
             [0,0,0,0,0,0,1,1,1,0,0,0,0,0,0,0],
             [0,0,0,0,0,0,0,1,1,0,0,0,0,0,0,0]]

nose_right = [[0,0,0,0,0,0,0,1,1,0,0,0,0,0,0,0],
              [0,0,0,0,0,0,0,1,1,1,0,0,0,0,0,0],
              [0,0,0,0,0,0,0,1,1,1,0,0,0,0,0,0],
              [0,0,0,0,0,0,0,1,1,0,0,0,0,0,0,0]]

nose_small = [[0,0,0,0,0,0,0,1,1,0,0,0,0,0,0,0],
              [0,0,0,0,0,0,0,1,1,0,0,0,0,0,0,0]]


blank = [[0,0,0,0,0,0,0,0,0,0,0,0,0,0,0,0]]

# faces

# happy face no nose
face_happy = 2 * blank + eyes_happy + 4 * blank + mouth_smile1 + 3 * blank
face_happy = numpy.array(face_happy)

# happy face with center nose
face_happy_nose1 = 2 * blank + eyes_happy + blank + nose_center + blank + mouth_smile2 + blank
face_happy_nose1 = numpy.array(face_happy_nose1)

# happy face with small nose
face_happy_nose2 = 2 * blank + eyes_happy + 2 * blank + nose_small + 2 * blank + mouth_smile2 + blank
face_happy_nose2 = numpy.array(face_happy_nose2)

# face looking up no nose
face_up = 2 * blank + eyes_up + 7 * blank + mouth_center + blank
face_up = numpy.array(face_up)

# face looking right no nose
face_right = 2 * blank + eyes_right + 7 * blank + mouth_right + blank
face_right = numpy.array(face_right)

# face looking right with nose
face_right_nose = 2 * blank + eyes_right + blank + nose_right + 2 * blank + mouth_right + blank
face_right_nose = numpy.array(face_right_nose)

# face looking left no nose
face_left = 2 * blank + eyes_left + 7 * blank + mouth_left + blank
face_left = numpy.array(face_left)

# face looking right with nose
face_left_nose = 2 * blank + eyes_left + blank + nose_left + 2 * blank + mouth_left + blank
face_left_nose = numpy.array(face_left_nose)

# face looking down no nose
face_down = 2 * blank + eyes_down + 7 * blank + mouth_straight + blank
face_down = numpy.array(face_down)

# face looking down with nose
face_down_nose = 2 * blank + eyes_down + 2 * blank + nose_down + 2 * blank + mouth_straight + blank
face_down_nose = numpy.array(face_down_nose)

# face looking down with smile
face_down_smile = 2 * blank + eyes_down + 4 * blank + mouth_smile1 + 3 * blank
face_down_smile = numpy.array(face_down_smile)

def set_pixels(face):
    unicorn.brightness(1.0)
    unicorn.off()
    for x in range(16):
        for y in range(16):
            h = 1.0
            s = 1.0
            v = face[x,y]
            r,g,b = colorsys.hsv_to_rgb(h, s, v)
            red = int(r*100.0)
            green = int(g*100)
            blue = int(b*100)
            unicorn.set_pixel(x, y, red, green, blue)
        unicorn.show()
        
try:        
    while True:
        set_pixels(face_happy)
        time.sleep (5)
        set_pixels(face_left)
        time.sleep (5)
        set_pixels(face_right)
        time.sleep (5)
        set_pixels(face_up)
        time.sleep (5)
        set_pixels(face_down)
        time.sleep (5)
        
finally:
    GPIO.cleanup()

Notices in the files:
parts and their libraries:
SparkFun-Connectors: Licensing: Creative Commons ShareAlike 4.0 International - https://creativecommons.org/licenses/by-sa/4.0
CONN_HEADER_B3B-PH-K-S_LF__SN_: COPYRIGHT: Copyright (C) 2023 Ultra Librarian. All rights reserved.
